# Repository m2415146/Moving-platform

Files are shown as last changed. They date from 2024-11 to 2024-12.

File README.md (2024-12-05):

# Moving-platform
Study task to make a moving platform  

## what we need to do  

  

  

  

## plan  

  

## printing Mounting for wheels  

  

slicing in OrcaSlicer  

  

This arrangement of the printing part at an angle is required in order to arrange the layers of the filament in order to better resist the load  

3d printer Creality Cr 10 SE, nozzle 0.4  

filament - PETg (Bestfilament)  

ready  

  

## Soldering  

There will be a link to  [Soldering first steps](https://github.com/m2415146/Soldering-first-steps- ) 

motor  

  

motor driver  

  

led stripe

photo_5348459913023712523_y  

the soldering points were covered with glue using a hot glue gun to protect them (since this was my first soldering and I had to be safe)  

photo_5348459913023712530_y  

## we fix the wheel holder to the motor  

fixation takes place using screws and nuts with a rubber stopper M3. Tighten with a screwdriver (for the screw), holding the nut with tongs  

photo_5348459913023712537_y  

photo_5348459913023712538_y  

check the fixation: the holder should not fall off from the motor  

https://github.com/user-attachments/assets/3da61deb-5c9a-44c5-a60f-2bdaaf4d3413  

result  

photo_5348459913023712539_y  

it is important not to confuse the side from which the nut will stand, otherwise it will not be possible to achieve a good fixation  

also, a classmate showed a more effective way to tighten the screw and nut with a screwdriver and forceps  

https://github.com/user-attachments/assets/a5bcaa66-fdb9-4a56-b90c-fc863f89c91e  

## we strengthen the wires for the battery  

since the wire from the battery holder (battery) is weak enough, it was necessary to strengthen it with special metal adapters. one part of the adapter must fit on the rubber part of the wire, it must be bent with special forceps for better grip. then use soldering to connect  

photo_5348459913023712560_y  

then I took the thermal insulation tube, cut off the right part to cover the protruding part of the metal adapter. to make it compress the wire better, I used a construction hair dryer  

photo_5348459913023712559_y  

photo_5348459913023712566_y  

result  

photo_5348459913023712560_y (1)  

## assembly of electronic components  

We have connected the motors and the battery pack to the ESP32 board

photo_5348459913023712610_y  

5 volt battery to power the microcontroller 

photo_5348459913023712611_y  

led stripe (there must have been some mistake here, perhaps at the soldering stage, since the strip did not work)  to port number 16  

photo_5348459913023712612_y  

now you can check the operation of the system by controlling the program from your smartphone, which is written by  [Azamat Tavitov](https://github.com/m112521)

https://github.com/user-attachments/assets/2fefd0cb-a193-42c6-81dc-f85d08bf1cc4    

## Creating a platform and cutting a wheels  

since by this point I was already impatient to test the platform in action and was too lazy to go for measuring tools, I used lidar in my iphone using the roulette application  

I measured the width of the board and the finished 3rd class, which we were given in our hands 

photo_5348459913023712676_y  

photo_5348459913023712675_y  

photo_5348459913023712674_y  

the platform and wheels had to be cut out of plywood 3 mm wide using a laser engraver  

I took the finished wheels file, removed the extra parts from it in RhinoCeros  

photo_5348459913023712678_y  

the size of the platform was modeled "by eye", as well as its simple shape was taken in order to quickly test the principle of movement in action  

the holes for the 3rd finished wheel were modeled "by eye" with a margin. fasteners for plastic ties were also modeled, with which the motors had to be fixed (the important point was that the structure should be able to be disassembled, without compromising the electronic ones  

photo_5348459913023712685_y  

then I exported the file to the CorelDRAW program in the format.dxf and prepared for laser trimming. The lines were grouped so that the machine would first cut out the inner holes and only then the outer contours  

photo_5348459913023712686_y  

laser cut in action  

https://github.com/user-attachments/assets/76141e67-dd14-4b72-9e3a-f2b1d9ca3f77  

result  

photo_5348459913023712706_y  

## assembling components on the platform  

it was performed using plastic ties. black - wide, white - narrow  

motors with wheels are fixed on the underside of the platform  

photo_5348459913023712713_y  

view from the upper side of the platform  

photo_5348459913023712712_y  

of course, it could have been made neater and more aesthetically pleasing. but the time of the lesson was coming to an end and I couldn't wait to see the work of the platform assembled so that next week I could continue to move further in my studies  

in order to secure the electronic components at the top of the platform, I used additional ties, which I placed crosswise  

photo_5348459913023712715_y  

we fix the electronic components by threading additional ties  

photo_5348459913023712714_y  

## wheel assembly  

the wheels were assembled using the black (outer) part of the rings, which we were provided with ready-made wheels that I cut out of plywood and fixed them to holders on motors that had previously been printed on a 3d printer. fixing took place with screws and nuts  

photo_5348459913023712677_y  

photo_5348459913023712729_y  

## checking the platform in motion 

The control is performed using an application written by [Azamat Tavitov](https://github.com/m112521)

https://github.com/user-attachments/assets/3c18ef59-5599-45ed-93f8-bce452537a43  

## new variations of movement  

first, I need to print out the adapters from the motors to the wheels. since I do this at home, I will use the materials that I have  

3d printer - FlashhForge A5M  

the mode in the vegetable slicer, perhaps the standard setting for Petg Generic Flashforge, nozzle 04  

  

then I will try to print eSUN Petg on a filament.  

photo_5357327998287733741_y  

but I'm having trouble printing the eSUN again.  I will probably have to calibrate the filament. For now, I'll take an already working filament - Petg Geeetech  

Printing in action  

https://github.com/user-attachments/assets/f44fa785-e492-484f-85e3-be6618feb486

Ready parts  

photo_5357436703909994633_y  

I have printed 4 more samples and will be looking for new possibilities for modifying rotational motion that can be tested on our platform.

modelling a basic part for wheel  

I opened the file holderFootprint and made a 3d object out of it in the RhinoCeros program with screw holes. I have taken the thickness of 3 mm so far, as well as the plywood from which we cut the wheels in class. I will try the first layer with this thickness, then I will change it in accordance with the shape to be moved  

  

## 1v of wheels  

the simplest version, it's just interesting to try. when I already put it on the seal, I thought that it was worth making the very area of contact with the surface longer.  

modelling in RhinoCeros. I slightly increased the thickness of the wheel itself to increase the area of contact with the surface , also trying to give strength to the wheel. I made holes that would include the caps from the tightening screws and at this stage realized that it was worth making the structure with the holders from the motors themselves monolithic. but I already have holders for the motors. perhaps I will also try to print the screws themselves - which will be in the form of bushings without threads and will be connected to the main part of the mower with glue

  

Slicing in OrcaSlicer. Same printer, same material, same settings.  

  

Printing in action  

https://github.com/user-attachments/assets/2ba48bd0-10f4-4e60-9bdc-1c9c61ac9585    

making a screws in RhinoCeros  

  

SLicing in Orcaslicer  

  

Same printer, material, settings. there is now video of printing because of low printing time  

there will be no photos of the result, since of the 3 printed screws, one was lost while I was removing it from the plate, the other had the screw cap broken off during removal, and the third, during an attempt to tighten, also broke - the cap broke off, and the rest of the screw had to be removed from the holes.  

I understood that the problem arises at the level of interlayer adhesion, but also because of the small size of the screw. therefore, I tried to arrange it differently on the printing platform and printed it again  

  

Same printer, material, settings.  

ready.  

photo_5361940303537366981_y  

https://github.com/user-attachments/assets/886e0990-b502-4e0f-98a5-97c16a9197d7  

failure again. for now, I'll give up trying to print screws of a similar size.  

since I couldn't apply the printed screws, I used metal ones.  

installing wheels to the platform  

https://github.com/user-attachments/assets/f6decfcf-3e91-49a7-ada4-5c3e19105132  

Ready  

photo_5373137459371698234_y  

Platform with wheels v1  

photo_5370778414224630648_y  

## 2v of wheels  

I find it interesting to move the rotation to another plane, so I started considering other options. I found a [gear project](https://www.printables.com/model/607786-bevel-gear-tester-with-parametric-gears)
gear project and decided to use it as a wheel.  

  

in order to get the necessary parts from the project, I used the RhinoCeros program. Also there I added the motor element itself with spherical legs at an angle  

  

  

for the convenience of printing, I did not combine the models and used them for slicing OrcaSlicer  

  

Same printer, material, settings  

Printing in action:  

https://github.com/user-attachments/assets/7beff7d0-a5b7-404e-8813-7f63a9586a19  

Ready  

photo_5361940303537367303_y  

since the printing of the first gears turned out well, I put the gears for the other wheel on the seal. I will need to think about the part that will connect the upper and lower gears.  

when I was thinking about it, I realized that it was possible to use a swivel joint, which I modeled in RhinoCeros  

  

  

Slicing in Orcaslicer, same printer, settings and nozzle. Printing was together with parts from whleel v3 parts  

  

photo_5361692999320463886_y  

when I installed them, one of the hinge holders broke, the other was fine. I will glue the broken one with methylacrylate glue  

photo_5361692999320463887_y

## 3v of wheels  

I continue experimenting with moving the axis of rotation to another plane. in this case, I want to move the wheels down and slightly to the side (which I did not reflect on the modeling, but it will be visible in the final assembly)  

Modelling in RHinoCeros. I added holes in the wheels to reduce weight and reduce the load on the axle, from which rotation will be transferred from the motor to the wheels

  

  

SLicing in OrcaSlicer. Same printer, material and settings but - completion 20% vs 15% before  

  

Ready  

photo_5361692999320463885_y  

When I printed the details, I noticed that I had made an axis with a large tolerance, on which the guide will be attached closer to the motor (I decided not to fix it), the cap for attaching to the axis of the wheel itself turned out to be small and I modeled it and printed it with the desired inner diameter. Also, the guide on the wheel side turned out to be quite thin from one edge and I will model a holder for it, which I will glue on top so that it gives strength  

## Platform v 2.0  

to solve a number of problems and implement some transportation options, it took the manufacture of a new version of the platform. it is characterized by a reduced size, as well as a large number of holes for fixing the necessary parts on the platform with screws  

Modelling in Rhinoceros8  

  

adaptation for laser cutting in CorelDRAW  

photo_5373137459371698223_y  

laser cutting  

https://github.com/user-attachments/assets/4c1fcbaf-7cb4-4839-9e15-85ec93b00da1  

Ready  

photo_5373137459371698224_y

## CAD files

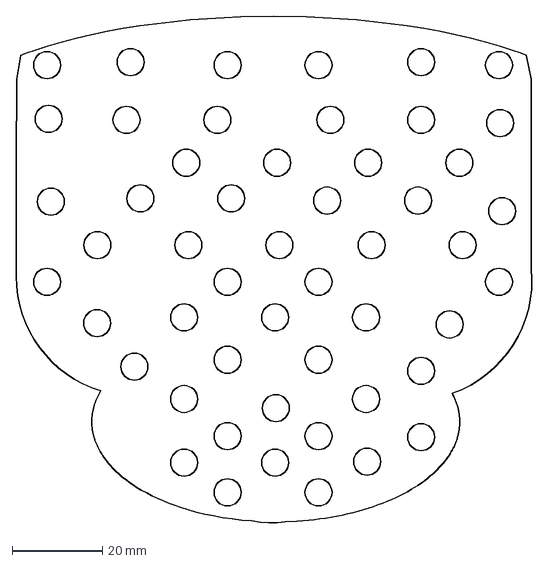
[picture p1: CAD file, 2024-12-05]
New_platform_plywood.dxf
115.3 x 112.4 mm

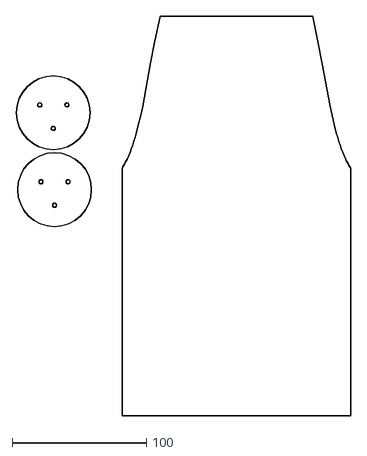
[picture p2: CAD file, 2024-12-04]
platform without holes.dxf
249.1 x 298.0

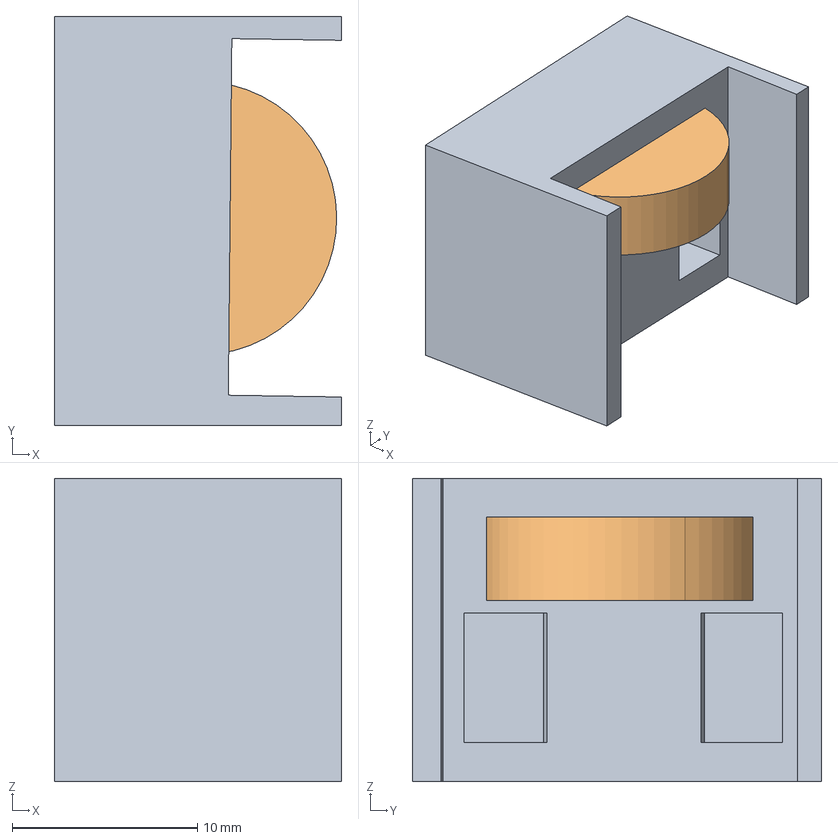
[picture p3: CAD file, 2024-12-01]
add4wheel3.stp
15.5 x 22.1 x 16.4 mm

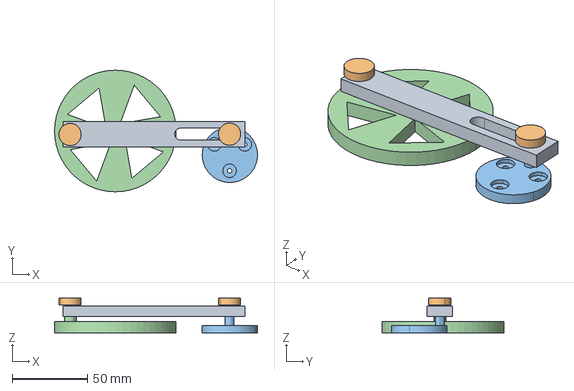
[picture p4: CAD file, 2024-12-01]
wheel3.stp
134.8 x 80.8 x 23.2 mm

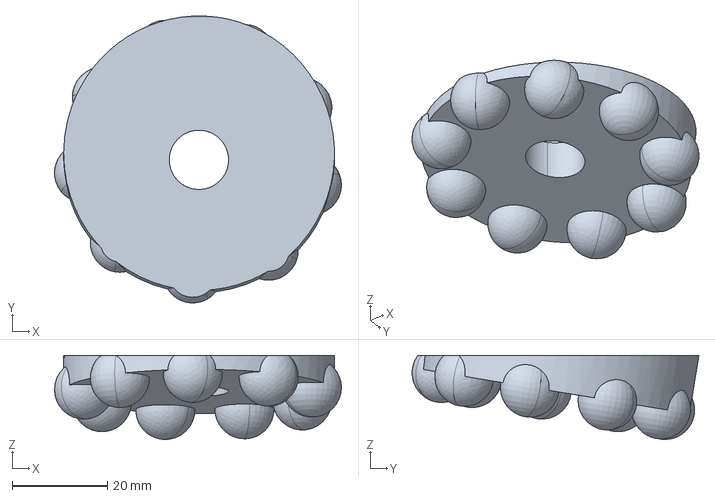
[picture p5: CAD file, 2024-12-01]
wheeltry2.stp
60.3 x 60.3 x 17.7 mm

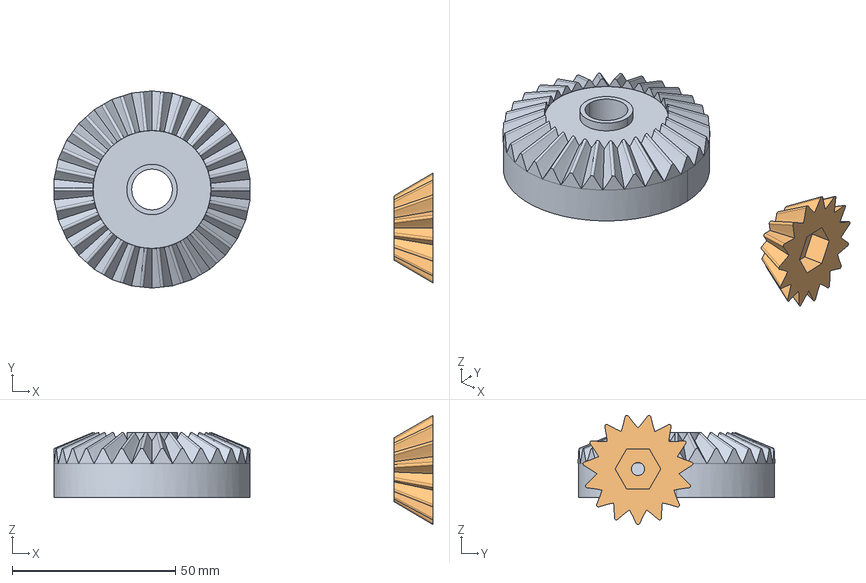
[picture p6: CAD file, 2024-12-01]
bearing2.stp
116.0 x 60.3 x 33.5 mm

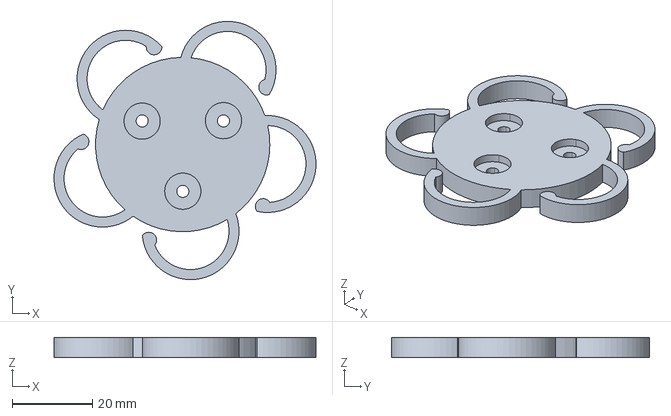
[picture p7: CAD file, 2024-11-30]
wheeltry1.stp
65.1 x 64.2 x 5.00 mm

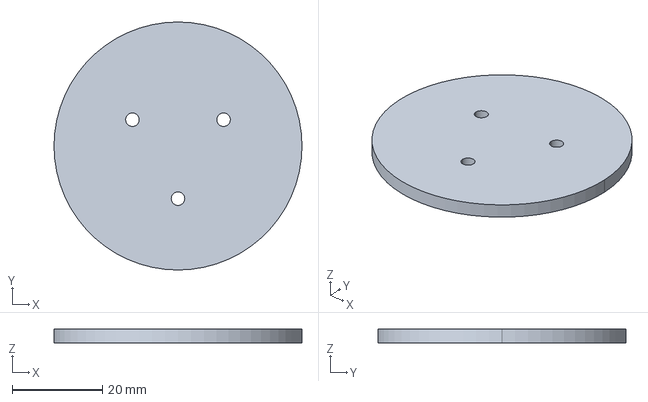
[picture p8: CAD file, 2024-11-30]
wheelbasicforplatform.stp
55.0 x 55.0 x 3.00 mm

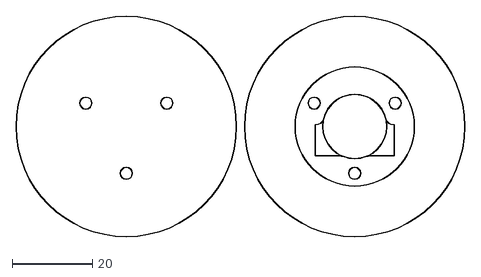
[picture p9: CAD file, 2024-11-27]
holderFootprint.dxf
112.0 x 55.0

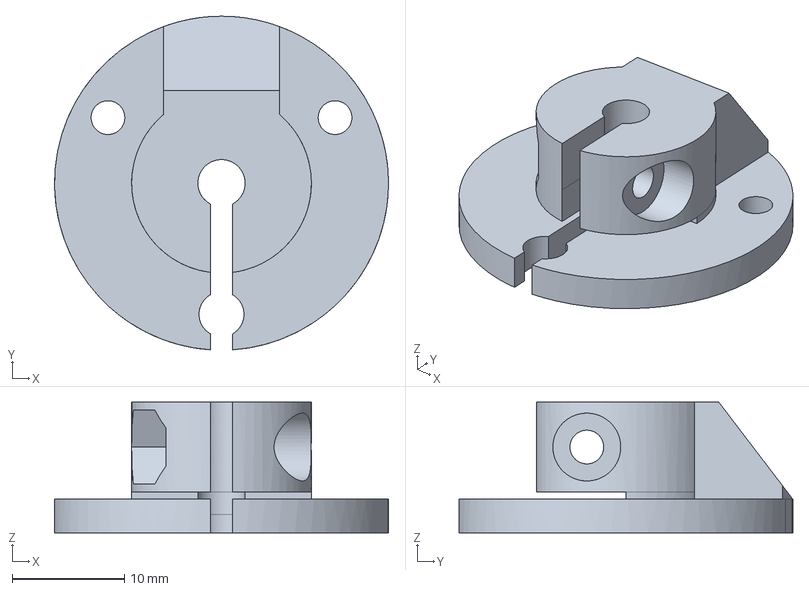
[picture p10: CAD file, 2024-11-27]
onShaftHolder.stp
29.7 x 29.7 x 11.6 mm

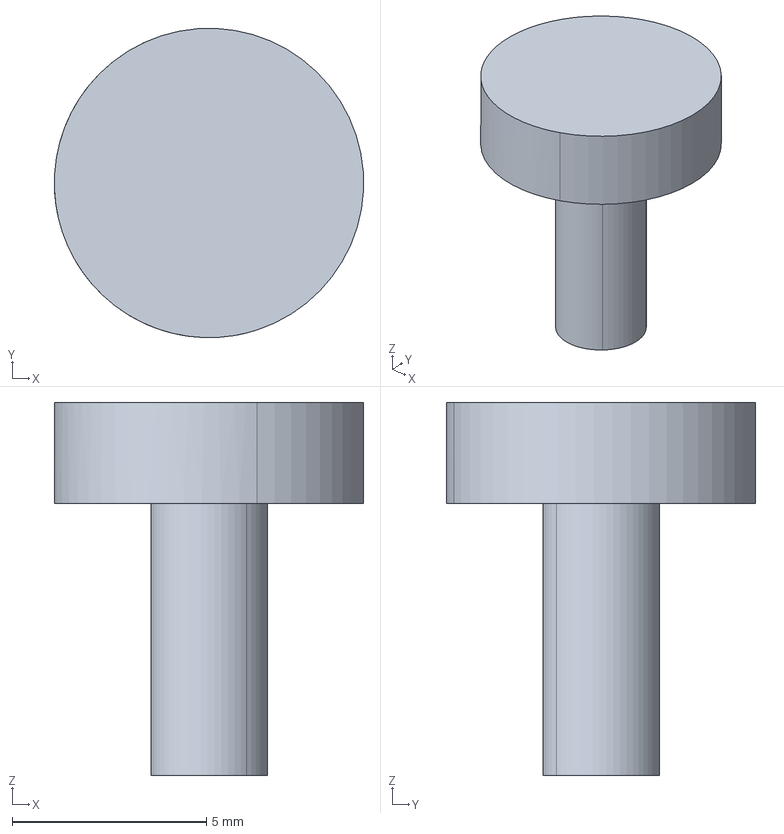
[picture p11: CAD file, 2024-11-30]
screw4wheel1.stp
7.95 x 7.96 x 9.60 mm

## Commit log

2024-11-27 Add soldering.md
2024-11-27 Soldering and electronic components.md
2024-11-30 Add home printed holders.md
2024-11-30 add basic wheel.md
2024-11-30 Add wheel v1.md
2024-11-30 add wheel v1
    [wheeltry1.stp]
2024-11-30 add screw1.md
2024-11-30 add screw for wheels
    [screw4wheel1.stp]
2024-11-30 add no video screw.md
2024-12-01 add gear.md
2024-12-01 Add printing gears.md
2024-12-01 add wheel3.md
2024-12-01 add wheel3
    [wheel3.stp]
2024-12-01 add comment about holes.md
2024-12-04 add platform witout holes file
    [platform without holes.dxf]
2024-12-05 Add new platform
    [New_platform_plywood.dxf]
2024-12-05 add instal wheels v1.md
